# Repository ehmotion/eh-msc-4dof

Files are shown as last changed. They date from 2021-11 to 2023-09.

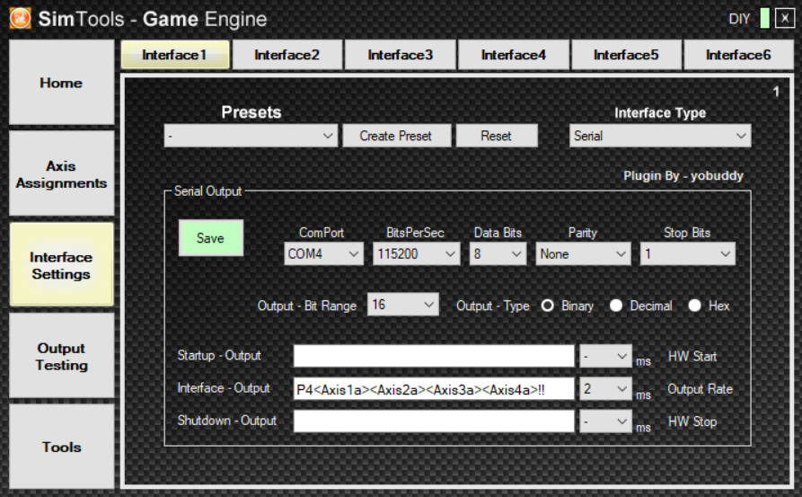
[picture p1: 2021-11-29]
simtools-port.png

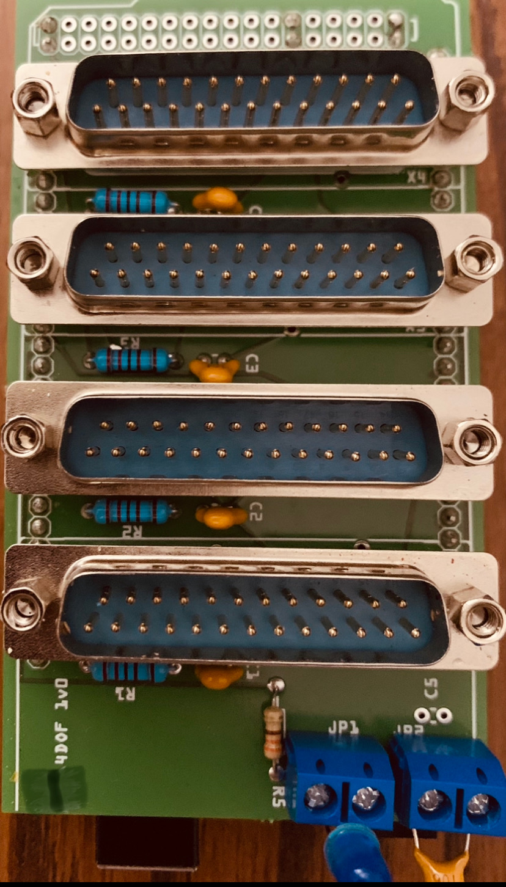
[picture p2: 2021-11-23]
board.jpg

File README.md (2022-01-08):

# eh-msc-4dof

4 channel servo controller code for Arduino Mega 2560 for AASD-15A and similar motor driver

Arduino sketch for generating pulses needed to control servo drivers such as the AASD-15A used in the SFX100 project and the pt-actuators.<br>
The controller is meant for the SFX100 actuator and the likes but it could easily be adapted to other configurations.

# v1 - uses range detection
The controller will start detecting your actuator limits as soon as it is powered on so make sure you have all required connections ready prior to power on.<br>

# v2 - uses specified stroke
```
#define STROKE_LIMIT  100               //100mm limit means we do no homing
```
Use the stroke length you want, keep in mind that this should be in line with your actuator stroke so make sure you measure it.
The circuit section between Arduino pin 18 (19, 20, 21) and DB25 pin 23 can be discarded since no limits detection is performed.

Both versions protect your actuators by not reaching their limit (it reserves 5mm at each end).
Both versions use 0..65535 positions and maps them to the actuator lenght.

<br>
The following connections are required:

```
AASD-15A
CN2 DB25 pin / Arduino pin
Motor 1
 3              12
 4              A0
 6              A4
 23             18 (via 2.2kohm resistor and 0.1uF capacitor to GND)
 9              5Vcc
 5,10,14        GND

Motor 2
 3              2
 4              A1
 6              A5
 23             19 (via 2.2kohm resistor and 0.1uF capacitor to GND)
 9              5Vcc
 5,10,14        GND

Motor 3
 3              7
 4              A2
 6              A6
 23             20 (via 2.2kohm resistor and 0.1uF capacitor to GND)
 9              5Vcc
 5,10,14        GND

Motor 4
 3              45
 4              A3
 6              A7
 23             21 (via 2.2kohm resistor and 0.1uF capacitor to GND)
 9              5Vcc
 5,10,14        GND
```
!!!WARNING: failure to make the proper connections may result in broken actuators.<br>
<br>
!!!If this is your first time, try one actuator at a time in each port since it won't mind if any of them is not connected. Watch the serial console/monitor in Arduino IDE to follow what happens during limits detection (the LED flashes slowly).

-the torque reach signal requires the following connection:
```
CN2 DB25 pin 23 -- 2.2kohm resistor -- Arduino pin
                \-- 0.1uF capacitor -- GND<br>
(resistor between DB25 pin 23 and Arduino; capacitor between DB25 pin 23 and GND)
```
The following parameters are required for the AASD 15A controller:<br>
(push MOD until you see Pn000 to enter the parameter setup mode)
```
Pn2 = 2
Pn8 = 300
Pn9 = -300
Pn51 = 3000 (motor top speed/rpm, could be run slower if wanted)
Pn98 = 10
Pn109 = 1
Pn110 = 30
Pn113 = 20
Pn114 = 10
Pn115 = 100
Extra parameters needed in the AASD-15A drivers used for limits detection:
Pn24 = 100 (reach predetermined torque > 100%)
Pn52 = 1
Pn60 = 2 (not used for now)
Pn61 = 6

AASD-15A CN2 DB25 control signal connector explained:
 p3 - pwm signal
 p4 - direction
 p5 - GND
 p6 - enable (motor ON)
 p9 - 5Vcc
p10 - GND
p11 - ready (motor present and ready - not used for now)
p14 - GND
p23 - torque reached
```
Message format used for position control in FlyPTMover (starts with 'P4', ends with '!!'):
```
P4<Axis1a><Axis2a><Axis3a><Axis4a>!!
```
Serial port configuration: 115200,8N1<br>
Command speed frequency: 2ms<br>
Position data: 2 bytes binary<br>
Position encoding: 16bits<br>
Check the screenshots for details on FlyPTMover / Simtools settings.

Position control range: 0 to 65535 - it gets mapped to actuator limits as detected on power on.<br>
To avoid limit detection for each serial port access, use a 10uF capacitor between Arduino pins RESET and GND.<br>
Note that it is no longer possible to upload the sketch on the Arduino while the capacitor is connected.<br>

Thanks to cubexvr! based on https://github.com/cubexvr/servoController

ENJOY at your own risk!

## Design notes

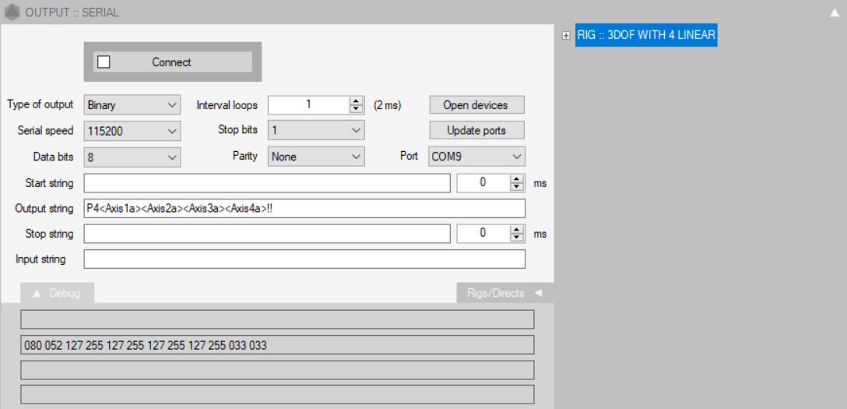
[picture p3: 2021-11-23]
flyptmover-port.png

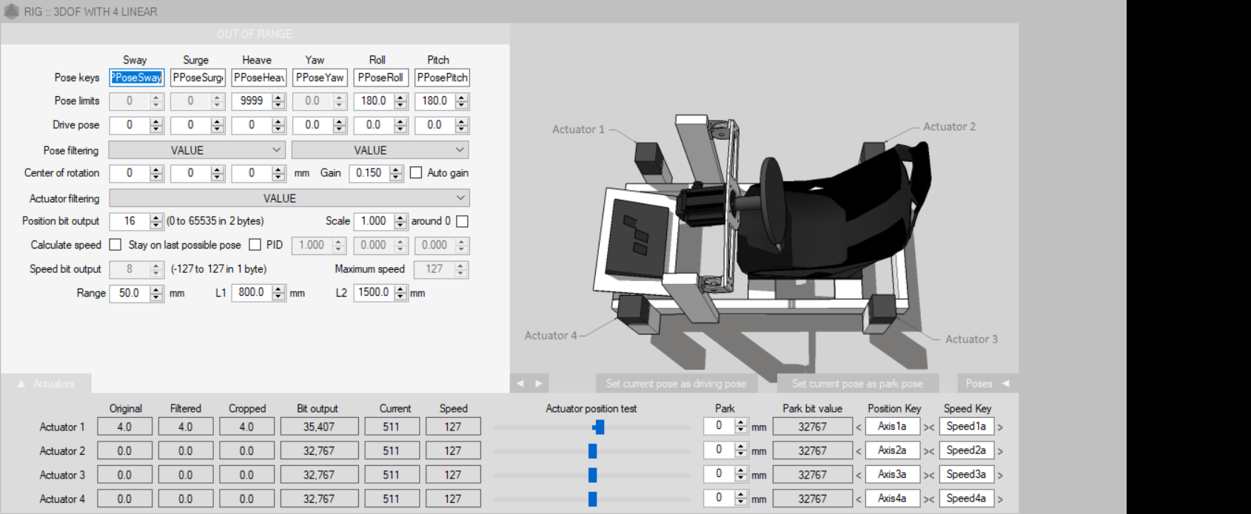
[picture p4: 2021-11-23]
flyptmover-rig.png

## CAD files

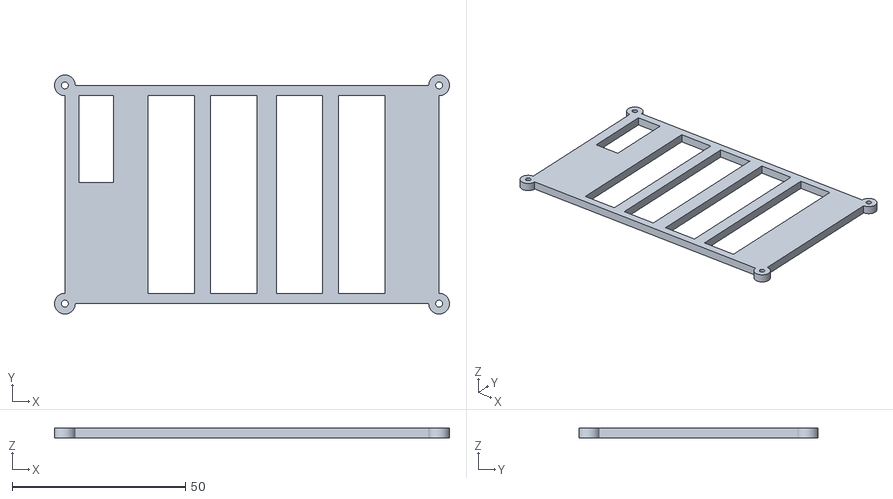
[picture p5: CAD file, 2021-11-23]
3dmodel-top.stl
114.0 x 69.0 x 3.00

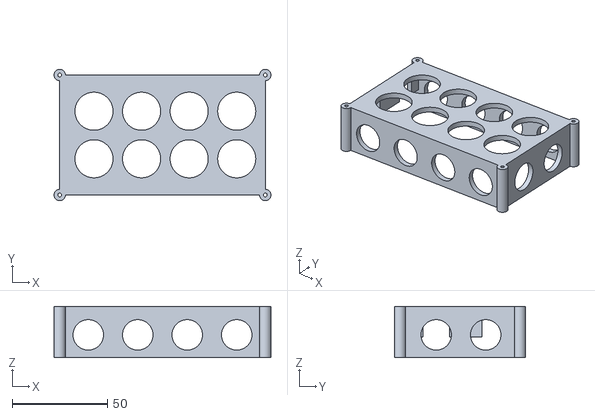
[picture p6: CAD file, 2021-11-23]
3dmodel-case.stl
114.0 x 69.0 x 27.0

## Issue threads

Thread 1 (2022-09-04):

About v1 and v2 difference.

1248280302, 2022-09-04:
It seems that v2 increases the stroke setting. Does it mean that one section uses the torque reached signal to achieve zero point, and the other end directly defines the precise stroke? The stroke range of the v1 is that both ends use the torque reached signal to determine the stroke?

ehmotion, 2022-09-04:
that's correct: v1 detects the stroke length whereas v2 takes it as given and considers the 'power on' position to be 0.

1248280302, 2022-09-04:
> That's correct: v1 detects the stroke length whereas v2 takes it as given and considers the 'power on' position to be 0. Position 0 is considered when the actuator is fully collapsed (as opposed to maximum position when fully extended).
>
> Make sure to measure your actuator's stroke when using v2 and set the right value in milimeters for: #define STROKE_LIMIT 100 //100mm limit means we do no homing

Well.So v1 depends on the two torque arrival signals generated at both ends to determine the range? Does v2 need to be manually pushed down to zero before 'power on' each time?

ehmotion, 2022-09-04:
Yes, v2 considers position 0 to be the current position when power is applied, then it 'homes' to the middle of the STROKE length, hence the need to have the actuator fully collapsed when it is powered on.
If you use it on a regular platform as vertical actuator, the platform weight takes care of the collapse of actuators but I have the feeling you don't use it as regular actuator, right? What do you use it for?

1248280302, 2022-09-09:
> Yes, v2 considers position 0 to be the current position when power is applied, then it 'homes' to the middle of the STROKE length, hence the need to have the actuator fully collapsed when it is powered on. If you use it on a regular platform as vertical actuator, the platform weight takes care of the collapse of actuators but I have the feeling you don't use it as regular actuator, right? What do you use it for?

Well, I want to use 4 actuators on the 3DOF simulator. Each corner of the rectangular frame is configured with one, which should be a regular shape.

1248280302, 2022-09-11:
@ehmotion
I viewed the code. In addition to adding a specific travel limit, can V2 also use the torque arrival signal?
 I want to use the hall switch instead of the torque reached signal to realize automatic back to zero point after startup. Will V1 first rotate forward and reverse to detect the stroke after startup?

ehmotion, 2022-09-12:
v1 uses the torque reached signal, v2 doesn't.
v1 extends the actuator until the signal is reached, then retracts it until the signal is reached and this is how it computes the stroke length. if you follow the arduino serial monitor output, you'll see some info about the detection process.

1248280302, 2022-09-12:
> > Yes, v2 considers position 0 to be the current position when power is applied, then it 'homes' to the middle of the STROKE length, hence the need to have the actuator fully collapsed when it is powered on. If you use it on a regular platform as vertical actuator, the platform weight takes care of the collapse of actuators but I have the feeling you don't use it as regular actuator, right? What do you use it for?
>
> Well, I want to use 4 actuators on the 3DOF simulator. Each corner of the rectangular frame is configured with one, which should be a regular shape.

Well, I looked at the code and saw that there was also a safe [] interrupt in V2. I thought that V2 was to add the travel setting on the basis of V1, so I wanted to use this signal to realize automatic return to the origin when starting up.

#define SPD_HOMING 500.How is this value calculated?

#define HOMING_INC 2.What does the definition mean？

ehmotion, 2022-09-12:
v2 is based on v1 and most of the code is still there but it is unused.
SPD_HOMING is not computed, it is empirical based on my own experience and trying to avoid breaking the actuator when detecting its limits.
you can enable limit detection with v2 if you set the STROKE_LIMIT to 0 but I have not tested this. the main use of v2 is to avoid doing limit detection and hence avoid stressing the actuator at every startup.
the safe interrupt SHOULD disable the Arduino in case an actuator limit is reached during normal use, to avoid damaging the hardware.

1248280302, 2022-09-15:
@ehmotion
In your code:
TCNT1 = period - 1;
ICR1 = period; // Timer TOP
So will a count cause an interrupt from TCNTn to ICRn?

// 3us (should not be changed, timing is critical)
const unsigned int pulseLength = 5;
Why set OCRnB=pulseLength?Does this mean that the width of a single pulse varies from 0 to 5 intervals?But why is it 3us instead of 2.5us(5 periods×0.5us)?

ehmotion, 2022-09-21:
the original code belongs to https://github.com/cubexvr/servoController
I only adapted it for limits detection and configured it based on what is suitable for AASD15A controller.
I'm sure some answers are to be found in the ATMEGA datasheet.
I'm sorry I don't have a better answer.

1248280302, 2022-09-21:
@ehmotion Thanks!I'm reading the datasheet.

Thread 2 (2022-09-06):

Switch off in a controlled manner

dabohda, 2022-09-06:
How can the actuators be switched off again in a controlled manner? As soon as I start the Arduino, the actuators start up. But how can I shut them down again in a controlled way? Couldn't I use the start and stop string in FlyPT? Unfortunately I am not that good to implement this. Could you add the feature?

ehmotion, 2022-09-06:
Responded [here](https://www.xsimulator.net/community/threads/4dof-controller-code-for-arduino-mega-for-aasd-15a-and-similar-driver.14421/page-6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), but I'll copy the message for simplicity:

Try using stop position with something like: P4<0><0><0><0>!!
I'm hoping that's the way to tell FlyPT to send 0 position as I cannot currently test this.

Note that because of the end dead zones (the Arduino code will protect the actuator by not going all the way to the end), you may still feel a bit of a 'drop' to physical zero, but it should be very little.

ehmotion, 2022-09-09:
check development branch https://github.com/ehmotion/eh-msc-4dof/tree/dev/eh-msc-4dof_v2
there's a new command for moving the actuator using 'homing' speed: Ph<0><0><0><0>!!

zhai1987, 2022-09-10:
> check development branch https://github.com/ehmotion/eh-msc-4dof/tree/dev/eh-msc-4dof_v2 there's a new command for moving the actuator using 'homing' speed: Ph<0><0><0><0>!!
brother. Thank you very much for your modification. There is no problem with flypt settings. Can you also modify simtools? Every time you change the game, it will return to the original point and drive it again, it will rise quickly!

ehmotion, 2022-09-10:
I don't know about SimTools but you can try these:
Start: Ph<32768><32768><32768><32768>!!
Stop: Ph<0><0><0><0>!!

If it gets overridden too fast, try to set the Timing in SimTools to 5000ms right after the Output string for Start and Stop.

zhai1987, 2022-09-10:
> I don't know about SimTools but you can try these: Startup - Output: Ph<32768><32768><32768><32768>!! Shutdown - Output: Ph<0><0><0><0>!!
>
> If it gets overridden too fast, try to set the Timing in SimTools to 5000ms right after the Output string for Startup and Shutdown. This way it should allow 5 seconds for the move to finish before sending any other command.

Shutdown - output: pH < 0 > < 0 > < 0 > < 0 >!! The flypt settings are very useful. Because its in-game settings are activated,
In simtools, start every time you start the game! I'll try to start it later! Thank you!

zhai1987, 2022-09-10:
> I don't know about SimTools but you can try these: Startup - Output: Ph<32768><32768><32768><32768>!! Shutdown - Output: Ph<0><0><0><0>!!
>
> If it gets overridden too fast, try to set the Timing in SimTools to 5000ms right after the Output string for Startup and Shutdown. This way it should allow 5 seconds for the move to finish before sending any other command.

Brother, startup - output: pH &lt; 32768 &gt; &lt; 32768 &gt; &lt; 32768 &gt; &lt; 32768 &gt;!! It's still the same! The startup speed is very fast, thank you

ehmotion, 2022-09-12:
Make sure you use the right characters as it is case-sensitive: the first two are either "P4" or "Ph" (uppercase P, lowercase h), not "pH".

zhai1987, 2022-09-12:
> Startup - Output: Ph<32768><32768><32768><32768>!!
Startup - Output: doesn't work!
Thanks a lot for your help, I'm testing!

zhai1987, 2022-09-12:
> Make sure you use the right characters as it is case-sensitive: the first two are either "P4" or "Ph" (uppercase P, lowercase h), not "pH".

Startup - Output: Ph<Axis1a><Axis2a><Axis3a><Axis4a>!!
He is in flypt and can soft start, but not in SIMTOOLS
· very strange ·

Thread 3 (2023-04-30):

About the frequency of the output position pulse.

1248280302, 2023-04-30:
I viewed your code.
The frequency of this code turnover level is 50kHz maximum and 4kHz minimum. Is that right? Is the time from 0mm to 100mm 0.4s?

ehmotion, 2023-05-02:
in theory at least, yes. I've yet to run some timing measurement using a logic analyser to confirm. if you have one handy you can do that yourself.
I'm working on a test setup and I may be able to verify that in a few weeks.

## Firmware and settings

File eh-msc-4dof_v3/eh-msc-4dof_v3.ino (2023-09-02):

/*
Thanks to cubexvr! based on https://github.com/cubexvr/servoController

1 period = 0.5us

AASD 15A controller parameters:
Push MOD until you see Pn000. This enters the parameter mode.
Change and check these settings on all motors:

Pn2 = 2 - location control mode

Required params set-up
Pn8 = 300 Internal around are torque limit (CCW)
Pn9 = -300 Around inside the torque limit (the CW)
Pn51 = 1200 (3000) The motor running top speed limit
Pn98 = 10 - pulse multiplicator
Pn109 = 1 - smoothing, 1=fixed smoothing, 2=s-Shaped smoothing
Pn110 = 30 - Smoothing Filter Time
Pn113 = 20 - Feedforward %
Pn114 = 10 - Feedforward Filter Time (ms)
Pn115 = 100 - Gain %
--
Pn97 - reverse the motor direction (0=ccw, 1=cw) Instruction selection logic pulse input direction

Extra parameters needed in the AASD-15A drives are the following:
Pn24 = 100 reach predetermined torque > 100%
Pn52 = 1 SigIn1 port functional allocation  > 1/Servo enable
Pn60 = 2 SigOut1 port functional allocation > 2/Servo ready
Pn61 = 6 SigOut2 port functional allocation > 6/Treach

CN2 control signal connector
 p3 - pwm signal
 p4 - direction
 p5 - GND
 p6 - enable: motor ON
 p9 - 5Vcc
p10 - GND
p11 - ready: motor present and ready
p14 - GND
p23 - torque reach: motor blocked

*/
#include <Arduino.h>
//#define FAILSAFE //not useful if run at full speed
#define NO_ACT_CHECK
// 2ms = 0.5 us * 4000 (can be adapted to needs)
const unsigned int samplePeriod = 4000;

// 20us == 50kHz (should not be changed, faster is not possible)
#define SPD_HOMING  500  //slowest homing
//#define SPD_HOMING  250 //faster homing
#define SPD_FASTST  39
unsigned int minPeriod = SPD_FASTST;
const unsigned int maxPeriod = samplePeriod;

// 3us (should not be changed, timing is critical)
const unsigned int pulseLength = 5;

const unsigned int minPos = 0;
const unsigned int centerPos = 11000;
const unsigned int maxPos = 22000;

//msg format: P4aabbccdd!!
//flypt mover: P4<axis1><axis2><axis3><axis4>!!
const unsigned int startMark1 = 'P';
const unsigned int startMark2 = '4';
const unsigned int endMark1 = '!';
const unsigned int endMark2 = '!';

#define MAX_MOTORS 4
byte motors = 0;

volatile unsigned int targetPos[MAX_MOTORS];
volatile unsigned int currentPos[MAX_MOTORS];
volatile int incPos[MAX_MOTORS];
volatile boolean stopSignal[MAX_MOTORS];
volatile boolean isRunning[MAX_MOTORS];

volatile unsigned int targetInput[MAX_MOTORS];

/* Pins */

// pulse 0 -> cn2 m0 p3
const byte ocr1bPin = 12;
// pulse 1 -> cn2 m1 p3
const byte ocr3bPin = 2;
// pulse 2 -> cn2 m2 p3
const byte ocr4bPin = 7;
// pulse 3 -> cn2 m3 p3
const byte ocr5bPin = 45;

// direction 0 -> cn2 m0 p4
const byte dir0 = A0;//30;
// direction 1 -> cn2 m1 p4
const byte dir1 = A1;//31;
// direction 2 -> cn2 m2 p4
const byte dir2 = A2;//32;
// direction 3 -> cn2 m3 p4
const byte dir3 = A3;//33;

//motor enable 0 -> cn2 m0 p6
const byte ena0p = A4;
//motor enable 0 -> cn2 m1 p6
const byte ena1p = A5;
//motor enable 0 -> cn2 m2 p6
const byte ena2p = A6;
//motor enable 0 -> cn2 m3 p6
const byte ena3p = A7;

//todo: move these to bitfield
volatile byte safe0s = LOW;
volatile byte safe1s = LOW;
volatile byte safe2s = LOW;
volatile byte safe3s = LOW;
volatile byte safeOs = LOW;

//torque-reach 0 -> cn2 m0 p23
const byte safe0p = 18;
//torque-reach 0 -> cn2 m1 p23
const byte safe1p = 19;
//torque-reach 0 -> cn2 m2 p23
const byte safe2p = 20;
//torque-reach 0 -> cn2 m3 p23
const byte safe3p = 21;

#ifdef NO_ACT_CHECK
//motor presence 0 -> cn2 m0 p11
const byte pres0p = A8;
//motor presence 1 -> cn2 m1 p11
const byte pres1p = A9;
//motor presence 2 -> cn2 m2 p11
const byte pres2p = A10;
//motor presence 3 -> cn2 m3 p11
const byte pres3p = A11;

byte pres[] = {pres0p, pres1p, pres2p, pres3p};
#endif

byte ena[] = {ena0p, ena1p, ena2p, ena3p};
byte safe[] = {safe0p, safe1p, safe2p, safe3p};

byte dir[] = {dir0, dir1, dir2, dir3};
byte pulse[] = {ocr1bPin, ocr3bPin, ocr4bPin, ocr5bPin};

// fast digital write for direction pins D30..D33
//#define setDirDown(b) PORTC |= (b)
//#define setDirUp(b) PORTC &=~ (b)
//-using analog pins A0..A3 for dir control
#define setDirDown(b) PORTF |= (b)
#define setDirUp(b) PORTF &=~ (b)
const byte dir0bit = B00000001;
const byte dir1bit = B00000010;
const byte dir2bit = B00000100;
const byte dir3bit = B00001000;

//const byte dir0bit = B10000000;
//const byte dir1bit = B01000000;
//const byte dir2bit = B00100000;
//const byte dir3bit = B00010000;

// faster may be possible, but is not needed
const unsigned long baudRate = 115200;

#define SerialC Serial
#define SerialD Serial3
#define SerialDbg Serial

#define DEBUG 1
#define debug_println(...) \
            do { if (DEBUG) SerialDbg.println(__VA_ARGS__); } while (0)
#define debug_print(...) \
            do { if (DEBUG) SerialDbg.print(__VA_ARGS__); } while (0)
#define debug_printf(...) \
            do { if (DEBUG) SerialDbg.printf(__VA_ARGS__); } while (0)
#define debug2_println(...) \
            do { if (DEBUG==2) SerialDbg.println(__VA_ARGS__); } while (0)
#define debug2_print(...) \
            do { if (DEBUG==2) SerialDbg.print(__VA_ARGS__); } while (0)

/* clock divider for timers /8 = 2MHz*/
const byte PRESCALE = B10;

// for direction pins
const bool UP = LOW;
const bool DOWN = HIGH;

volatile int kntr = 0;
const int led_pin = 3;//LED_BUILTIN;

const int ST_IDLING = 0;
const int ST_HOMING = 1;
const int ST_MAXING = 2;
const int ST_CTRING = 3;
const int ST_RUNING = 4;
volatile byte run_state = ST_IDLING;
const unsigned int POS_HOME = 0;
const unsigned int POS_CNTR = 32767;    //not scaled, full range
const unsigned int POS_MAXI = 65535;    //not scaled, full range
const unsigned int RANGE_SAFE = 20000;  //safe maximum position, for 100mm stroke
const unsigned int RANGE_DZ   = 1000;   //dead zone at the end of the range:
                                        // each 200pos means 1 motor rotation, i.e. 5mm stroke
#define STROKE_LIMIT  100               // 100mm limit means we do no homing. use 0 for homing,
                                        // use other values at your own risk(!!!) but check RANGE_SAFE above
const unsigned int HOME_DELAY = 2000;
volatile byte motor_state[] = {ST_IDLING, ST_IDLING, ST_IDLING, ST_IDLING};
volatile unsigned int motor_mins[] = {POS_HOME + RANGE_DZ, POS_HOME + RANGE_DZ,
  POS_HOME + RANGE_DZ, POS_HOME + RANGE_DZ};
volatile unsigned int motor_maxs[] = {RANGE_SAFE - RANGE_DZ, RANGE_SAFE - RANGE_DZ,
  RANGE_SAFE - RANGE_DZ, RANGE_SAFE - RANGE_DZ};

#define HOMING_INC 2

void delay4int(int ms)
{
  for (int i = 0; i < ms; i++)
    delayMicroseconds(1000);
}

void fail_loop()
{
  debug_println ("#sON#");
  //going HIGH, stop everything, faster than a for cycle
  digitalWrite(ena[0], HIGH);
  stopSignal[0] = true; //stop motor
  digitalWrite(ena[1], HIGH);
  stopSignal[1] = true; //stop motor
  digitalWrite(ena[2], HIGH);
  stopSignal[2] = true; //stop motor
  digitalWrite(ena[3], HIGH);
  stopSignal[3] = true; //stop motor
  //
  safeOs = HIGH;
  while (1) //do nothing else here, wait for reset
  {
    //never get out, wait for reset
    digitalWrite(led_pin, HIGH);
    delay4int(100);
    digitalWrite(led_pin, LOW);
    delay4int(100);
  }
}

int motors_count()
{
#ifdef NO_ACT_CHECK
  motors = MAX_MOTORS;
  debug_print ("#ACTs used: ");
  debug_println (motors);
  return MAX_MOTORS;
#endif
  //
  motors = 0;
  //check connection to motors 0..1
  if (digitalRead(pres[0]))//NOK
  {
    debug_println ("#eM0!#");
    //fail_loop();
    debug_print ("#ACTs found: ");
    debug_println (motors);
    return motors;
  }
  motors = 1;
  if (digitalRead(pres[1]))//NOK
  {
    debug_println ("#eM1!#");
    //fail_loop();
    debug_print ("#ACTs found: ");
    debug_println (motors);
    return motors;
  }
  motors = 2;
  if (digitalRead(pres[2]))//NOK
  {
    debug_println ("#eM2!#");
    //fail_loop();
    debug_print ("#ACTs found: ");
    debug_println (motors);
    return motors;
  }
  motors = 3;
  if (digitalRead(pres[3]))//NOK
  {
    debug_println ("#eM3!#");
    //fail_loop();
    debug_print ("#ACTs found: ");
    debug_println (motors);
    return motors;
  }
  motors = 4;
  debug_print ("#ACTs found: ");
  debug_println (motors);
  
  return motors;
}

void motors_check()
{
  if (motors == 0)
    fail_loop();
  //check connection to motors 0..1
  #ifdef NO_ACT_CHECK
  return;
  #endif
  //
  if (digitalRead(pres[0]))//NOK
  {
    debug_println ("#eM0!#");
    fail_loop();
  }
  if (motors == 1)
    return;
  if (digitalRead(pres[1]))//NOK
  {
    debug_println ("#eM1!#");
    fail_loop();
  }
  if (motors == 2)
    return;
  if (digitalRead(pres[2]))//NOK
  {
    debug_println ("#eM2!#");
    fail_loop();
  }
  if (motors == 3)
    return;
  if (digitalRead(pres[3]))//NOK
  {
    debug_println ("#eM3!#");
    fail_loop();
  }
}

#if 0
void int_safetyOVR()
{
  if (safeOs == HIGH)
    return;
  //SerialC.println("#sON!");
  //failure! failure! failure!
  fail_loop();
}
#endif

void int_stop0()
{
  debug_print ("#M0!");
  debug_print (safe0s);
  debug_print ("#");
  if (safe0s == HIGH)
    return;
  safe0s = HIGH;
  //digitalWrite(ena[0], HIGH);
  if (run_state == ST_HOMING)
    stopSignal[0] = true; //stop motor
  #ifdef FAILSAFE
  else
  //if (0 && run_state != ST_HOMING)
  {
    digitalWrite(ena[0], HIGH);
    stopSignal[0] = true; //stop motor
    debug_println ("#M0S!#");
    fail_loop();
  }
  #endif
  //debug_println ("M0SonL");
}

void int_stop1()
{
  debug_print ("#M1!");
  debug_print (safe1s);
  debug_print ("#");
  if (safe1s == HIGH)
    return;
  safe1s = HIGH;
  //digitalWrite(ena[0], HIGH);
  if (run_state == ST_HOMING)
    stopSignal[1] = true; //stop motor
  #ifdef FAILSAFE
  else
  //if (0 && run_state != ST_HOMING)
  {
    digitalWrite(ena[1], HIGH);
    stopSignal[1] = true; //stop motor
    debug_println ("#M1S!#");
    fail_loop();
  }
  #endif
  //debug_println ("M1SonL");
}

void int_stop2()
{
  debug_print ("#M2!");
  debug_print (safe2s);
  debug_print ("#");
  if (safe2s == HIGH)
    return;
  safe2s = HIGH;
  //digitalWrite(ena[0], HIGH);
  if (run_state == ST_HOMING)
    stopSignal[2] = true; //stop motor
  #ifdef FAILSAFE
  else
  //if (0 && run_state != ST_HOMING)
  {
    digitalWrite(ena[2], HIGH);
    stopSignal[2] = true; //stop motor
    debug_println ("#M2S!#");
    fail_loop();
  }
  #endif
  //debug_println ("M2SonL");
}

void int_stop3()
{
  debug_print ("#M3!");
  debug_print (safe3s);
  debug_print ("#");
  if (safe3s == HIGH)
    return;
  safe3s = HIGH;
  //digitalWrite(ena[0], HIGH);
  if (run_state == ST_HOMING)
    stopSignal[3] = true; //stop motor
  #ifdef FAILSAFE
  else
  //if (0 && run_state != ST_HOMING)
  {
    digitalWrite(ena[3], HIGH);
    stopSignal[3] = true; //stop motor
    debug_println ("#M3S!#");
    fail_loop();
  }
  #endif
  //debug_println ("M3SonL");
}
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
void loop()
{
  motors_check ();
  switch (run_state)
  {
    case ST_IDLING:
      minPeriod = SPD_HOMING;
      run_state = ST_HOMING;
      #if 0
      if (motors > 0)
        motor_printX (0);
      if (motors > 1)
        motor_printX (1);
      if (motors > 2)
        motor_printX (2);
      if (motors > 3)
        motor_printX (3);
      #endif
      homing_start ();
      if (0)
      {
        run_state = ST_RUNING;
        motor_parkX (0);
        motor_parkX (1);
      }
    break;
    case ST_HOMING:
    {
      if (homing_done())
      {
        minPeriod = SPD_FASTST;
        run_state = ST_RUNING;
        if (motors > 0)
          motor_parkX (0);
        if (motors > 1)
          motor_parkX (1);
        if (motors > 2)
          motor_parkX (2);
        if (motors > 3)
          motor_parkX (3);
        debug_print("\n>>");
        debug_print(motors);
        debug_println("ACT ready");
        //cleanup the serial line
        while (SerialC.available())
        {
          //digitalWrite(led_pin, HIGH);
          SerialC.read();
          //delay4int (100);
          //digitalWrite(led_pin, LOW);
          //delay4int (100);
        }
        digitalWrite(led_pin, HIGH);
        ledk = 0;
      }
      else
        ledk_act(20000/HOMING_INC, 1);
    }
    break;
    case ST_RUNING:
      if (SerialC.available())
      {
        //digitalWrite(led_pin, LOW);
        ledk_act (20, 1);//20 is good LED effect for 2ms flow
        command_check ();
      }
      else
        ledk_act (20, 0);
    break;
  }
}

uint16_t cmap_uint16 (uint32_t x, uint32_t in_min, uint32_t in_max, uint32_t out_min, uint32_t out_max)
{
  uint32_t rv = (x - in_min) * (out_max - out_min) / (in_max - in_min) + out_min;
  if (rv > out_max)
    rv = out_max;
  if (rv < out_min)
    rv = out_min;
  debug2_print ("Pm ");
  debug2_print (x, DEC);
  debug2_print (" > ");
  debug2_println (rv, DEC);
  return (uint16_t)rv;
}

//map position request to motor range
//- ditribute the 0..65535 interval to our motor's range
unsigned int mapToRangeX(int X, unsigned int pos)
{
  return cmap_uint16 (pos, POS_HOME, POS_MAXI, motor_mins[X], motor_maxs[X]);
}

unsigned int mapToRange(unsigned int pos)
{
  unsigned int mappedPos = pos / 3;
  if (mappedPos > maxPos)
  {
    return maxPos;
  }
  return mappedPos;
}


void initTimers() {
  // disable everything that we don't need, probably not needed
  PCICR = 0;
  PCMSK0 = 0;
  PCMSK1 = 0;
  PCMSK2 = 0;
  WDTCSR = 0;

  // disable 8 bit timers
  TIMSK0 = 0;
  TIFR0 = 0;
  TCCR0A = 0;
  TCCR0B = 0;
  TCNT0 = 0;
  OCR0A = 0;

  TIMSK2 = 0;
  TIFR2 = 0;
  TCCR2A = 0;
  TCCR2B = 0;
  TCNT2 = 0;
  OCR2A = 0;

  // The 16 bit timers that are used for generating the pulses
  TCNT1 = 0;
  OCR1A = 0;
  OCR1B = pulseLength;
  TCCR1A = 0;
  TCCR1B = 0;
  ICR1 = 0;
  TIMSK1 = 0;
  TIFR1 = 0;

  TCNT3 = 0;
  OCR3A = 0;
  OCR3B = pulseLength;
  TCCR3A = 0;
  TCCR3B = 0;
  ICR3 = 0;
  TIMSK3 = 0;
  TIFR3 = 0;

  TCNT4 = 0;
  OCR4A = 0;
  OCR4B = pulseLength;
  TCCR4A = 0;
  TCCR4B = 0;
  ICR4 = 0;
  TIMSK4 = 0;
  TIFR4 = 0;

  TCNT5 = 0;
  OCR5A = 0;
  OCR5B = pulseLength;
  TCCR5A = 0;
  TCCR5B = 0;
  ICR5 = 0;
  TIMSK5 = 0;
  TIFR5 = 0;
}

void stopTimer(byte motor) {
  switch (motor) {
    case 0:
      TCCR1B = B00011000;
      TIMSK1 = 0;
      //isRunning[0] = false;
      break;
    case 1:
      TCCR3B = B00011000;
      TIMSK3 = 0;
      isRunning[1] = false;
      break;
    case 2:
      TCCR4B = B00011000;
      TIMSK4 = 0;
      isRunning[2] = false;
      break;
    case 3:
      TCCR5B = B00011000;
      TIMSK5 = 0;
      isRunning[3] = false;
      break;
  }
}

void startTimerWithCrop(byte motor, unsigned int period)
{
  if (period < minPeriod)
  {
    period = minPeriod;
  }
  else if (period > maxPeriod)
  {
    period = maxPeriod;
  }
  startTimer(motor, period);
}

void startTimer(byte motor, unsigned int period)
{
  if (0)
  {
    debug_print("TMR");
    debug_print(motor, DEC);
    debug_print(" per ");
    debug_println(period, DEC);
  }
  switch (motor)
  {
    case 0:
      TCNT1 = period - 1;
      ICR1 = period; // Timer TOP
      TIMSK1 |= (1 << OCIE1A); // oca interrupt when counter = 0
      // fast PWM mode, clear ocr bits on compare match
      TCCR1A = B10101010;
      TCCR1B = B00011000 | PRESCALE;
      break;
    case 1:
      TCNT3 = period - 1;
      ICR3 = period; // Timer TOP
      TIMSK3 |= (1 << OCIE3A); // oca interrupt when counter = 0
      // fast PWM mode, clear ocr bits on compare match
      TCCR3A = B10101010;
      TCCR3B = B00011000 | PRESCALE;
      break;
    case 2:
      TCNT4 = period - 1;
      ICR4 = period; // Timer TOP
      TIMSK4 |= (1 << OCIE4A); // oca interrupt when counter = 0
      // fast PWM mode, clear ocr bits on compare match
      TCCR4A = B10101010;
      TCCR4B = B00011000 | PRESCALE;
      break;
    case 3:
      TCNT5 = period - 1;
      ICR5 = period; // Timer TOP
      TIMSK5 |= (1 << OCIE5A); // oca interrupt when counter = 0
      // fast PWM mode, clear ocr bits on compare match
      TCCR5A = B10101010;
      TCCR5B = B00011000 | PRESCALE;
      break;
  }
}

void move0(unsigned int target) {
  if (targetPos[0] != target) {
    if (isRunning[0]) {
      stopSignal[0] = true;
      while (isRunning[0]) {
        ;
      }
    }
    stopSignal[0] = false;
    unsigned int current = currentPos[0];
    if (target != current) {
      if (target > current) {
        setDirUp(dir0bit);
        incPos[0] = 1;
        targetPos[0] = target;
        isRunning[0] = true;
        startTimerWithCrop(0, samplePeriod / (target - current));
      } else {
        setDirDown(dir0bit);
        incPos[0] = -1;
        targetPos[0] = target;
        isRunning[0] = true;
        startTimerWithCrop(0, samplePeriod / (current - target));
      }
    }
  }
}

void move1(unsigned int target) {
  if (targetPos[1] != target) {
    if (isRunning[1]) {
      stopSignal[1] = true;
      while (isRunning[1]) {
        ;
      }
    }
    stopSignal[1] = false;
    unsigned int current = currentPos[1];
    if (target != current) {
      if (target > current) {
        setDirUp(dir1bit);
        incPos[1] = 1;
        targetPos[1] = target;
        isRunning[1] = true;
        startTimerWithCrop(1, samplePeriod / (target - current));
      } else {
        setDirDown(dir1bit);
        incPos[1] = -1;
        targetPos[1] = target;
        isRunning[1] = true;
        startTimerWithCrop(1, samplePeriod / (current - target));
      }
    }
  }
}
#if 1
void move2(unsigned int target) {
  if (targetPos[2] != target) {
    if (isRunning[2]) {
      stopSignal[2] = true;
      while (isRunning[2]) {
        ;
      }
    }
    stopSignal[2] = false;
    unsigned int current = currentPos[2];
    if (target != current) {
      if (target > current) {
        setDirUp(dir2bit);
        incPos[2] = 1;
        targetPos[2] = target;
        isRunning[2] = true;
        startTimerWithCrop(2, samplePeriod / (target - current));
      } else {
        setDirDown(dir2bit);
        incPos[2] = -1;
        targetPos[2] = target;
        isRunning[2] = true;
        startTimerWithCrop(2, samplePeriod / (current - target));
      }
    }
  }
}

void move3(unsigned int target) {
  if (targetPos[3] != target) {
    if (isRunning[3]) {
      stopSignal[3] = true;
      while (isRunning[3]) {
        ;
      }
    }
    stopSignal[3] = false;
    unsigned int current = currentPos[3];
    if (target != current) {
      if (target > current) {
        setDirUp(dir3bit);
        incPos[3] = 1;
        targetPos[3] = target;
        isRunning[3] = true;
        startTimerWithCrop(3, samplePeriod / (target - current));
      } else {
        setDirDown(dir3bit);
        incPos[3] = -1;
        targetPos[3] = target;
        isRunning[3] = true;
        startTimerWithCrop(3, samplePeriod / (current - target));
      }
    }
  }
}
#endif
// timing is critical, change nothing here
ISR(TIMER1_COMPA_vect, ISR_BLOCK) {
  //debug_println ("M0tmr");
  currentPos[0] += incPos[0];
  if (stopSignal[0] || currentPos[0] == targetPos[0]) {
    TCCR1B = B00011000;
    TIMSK1 = 0;
    isRunning[0] = false;
    if (0)
    {
      debug_print ("M0Etmr ");
      debug_println (currentPos[0], DEC);
    }
  }
}

ISR(TIMER3_COMPA_vect, ISR_BLOCK) {
  currentPos[1] += incPos[1];
  if (stopSignal[1] || currentPos[1] == targetPos[1]) {
    TCCR3B = B00011000;
    TIMSK3 = 0;
    isRunning[1] = false;
    if (0)
    {
      debug_print ("M1Etmr ");
      debug_println (currentPos[1], DEC);
    }
  }
}

#if 1
ISR(TIMER4_COMPA_vect, ISR_BLOCK) {
  currentPos[2] += incPos[2];
  if (stopSignal[2] || currentPos[2] == targetPos[2]) {
    TCCR4B = B00011000;
    TIMSK4 = 0;
    isRunning[2] = false;
  }
}
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

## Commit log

2021-11-23 add board picture
2021-11-23 add 3d model case
    [3dmodel-case.stl, 3dmodel-top.stl]
2021-12-23 detect limits using incremental position updates
    trying to avoid too much stress on the actuator when doing range detection/homing, now using increments of 2 positions
2022-01-05 added v2 with static stroke (no homing) 0 is start position
2023-08-28 add v3 for no stroke detection and no homing
2023-09-02 v2/v3 update actual pos limits to max; update LED feedback behavior
